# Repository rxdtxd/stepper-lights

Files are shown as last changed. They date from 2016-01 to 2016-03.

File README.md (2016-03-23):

# stepper-lights

## Table of Contents

* [Intro](#intro)
* [Using](#using)
  - [Warning](#warning)
  - [Overview](#overview)
  - [Schematics](#schematics)
  - [BOM](#bom)
  - [Fabrication files](#fabrication-files)
* [Modifying](#modifying)
  - [Toolchain](#toolchain)
  - [Custom symbols/footprints](#custom-symbolsfootprints)
* [Notes](#notes)
* [License](#license)

## Intro

Here's a project I did in early 2016 on controlling five stepper
motors with one AVR (Arduino Nano). Each channel has up/down
buttons and a potentiometer to control the speed.

## Using

### Warning

**I strongly suggest you do not try to recreate it verbatim, and use
as a guide at best.**

The schematics/layouts contained numerous glitches and therefore
impromptu fixes that were not propagated back to the design files.

Most notably, the used Arduino Nano symbol had its ADC pin order
reversed on the manufactured boards ([rev0.1](releases/tag/rev0.1)).
This required both hardware jumpering and software muckery, somewhat
reflected in [rev0.2](releases/tag/rev0.2).

Furthermore, the overall design leaves much to be desired. With
the current prices for Arduino Nano clones, **this should have been
a one-AVR-one-driver schematic**.

However, in the spirit of megalomania, I hereby release the files
under free licenses (for which see the bottom).

### Overview

There are two parts to the system: `controller` and `driver`:

```
             +-> driver
             |
             +-> driver
             |
controller --+-> driver
             |
             +-> driver
             |
             +-> driver
```

Communication is essentially single-directional SPI over RS422,
with the driver transmitting back a dummy message (i.e. no
feedback).

### Schematics

See [controller.png](schem/controller.png) and
[driver.png](schem/driver.png).

### BOM

See [controller.bom](schem/controller.bom) and
[driver.bom](schem/driver.bom).

Some mechanical components are not listed:

* push-buttons (OFF-(ON))
* power supply (24 V, 2+ A)
* power switch (OFF-ON)
* cooling fans (24 V)
* CAT6 cables and RJ45 connectors

### Fabrication files

See [fab](schem/fab) for gerbers and drill maps.

## Modifying

### Toolchain

The design files were produced on a [Arch](https://www.archlinux.org/)
GNU/Linux machine using [geda/gaf](http://www.geda-project.org/),
[pcb](http://pcb.geda-project.org/) and
[Emacs](https://www.gnu.org/software/emacs/).

AVR sources are built with [avr-gcc](https://gcc.gnu.org/). Arduino
is flashed with [avrdude](http://www.nongnu.org/avrdude/).

There are Makefiles for both schematics and code. Happy hacking!

### Custom symbols/footprints

...used in this project are available in my
[symbols](https://github.com/rxdtxd/geda-gschem-symbols-rxdtxd) and
[footprints](https://github.com/rxdtxd/geda-pcb-footprints-rxdtxd)
repos.

Note that these may have changed from the time they were used in the
project. I hope I was decent enough to change `symver`s and whatnot if
so.

## Notes

Some more unordered documentation is available in the [NOTES](NOTES)
file.

## License

Software in [src](src/) is licensed under [GPLv3](src/LICENSE). Hardware
designs in [schem](schem/) are licensed under [CERN OHL
v1.2](schem/LICENSE).

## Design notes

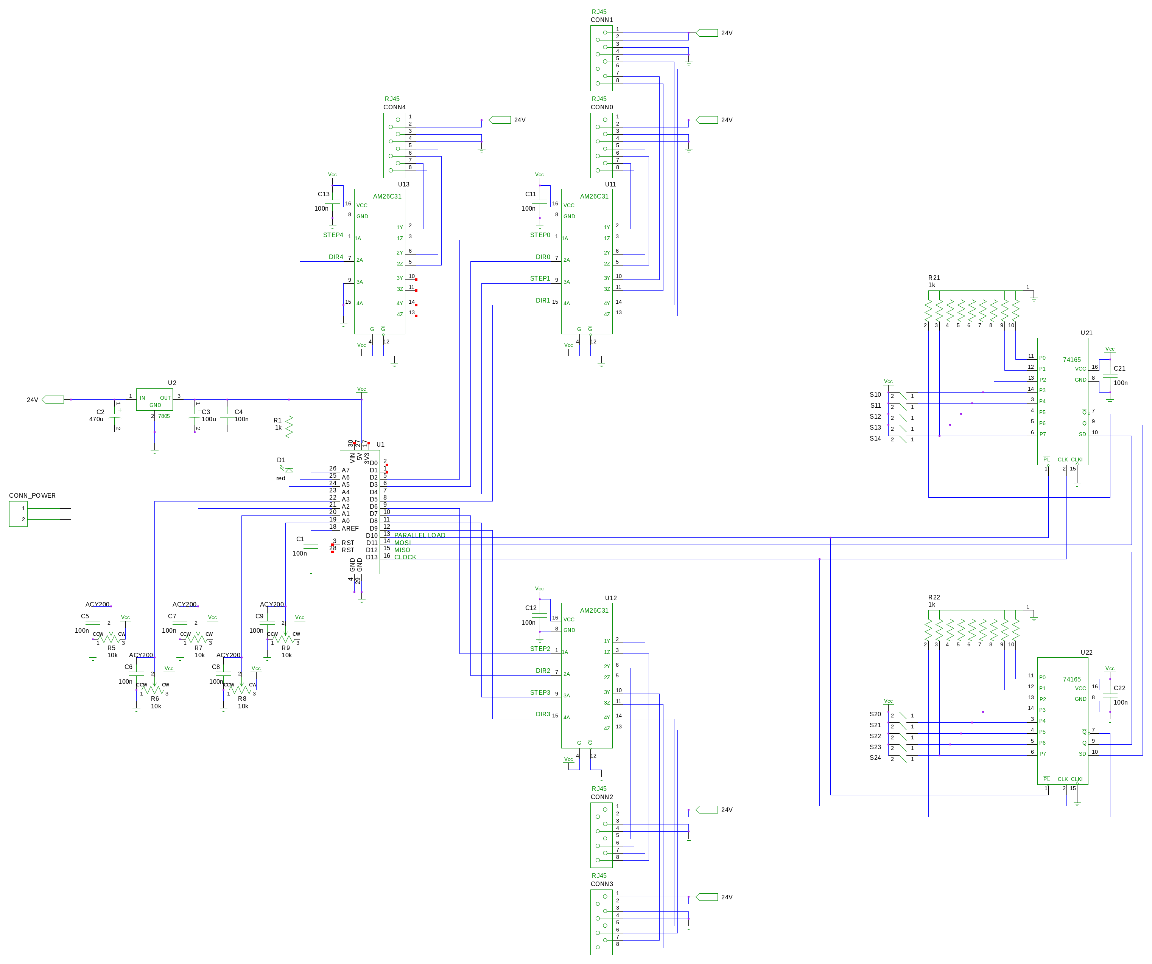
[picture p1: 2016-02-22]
schem/controller.png

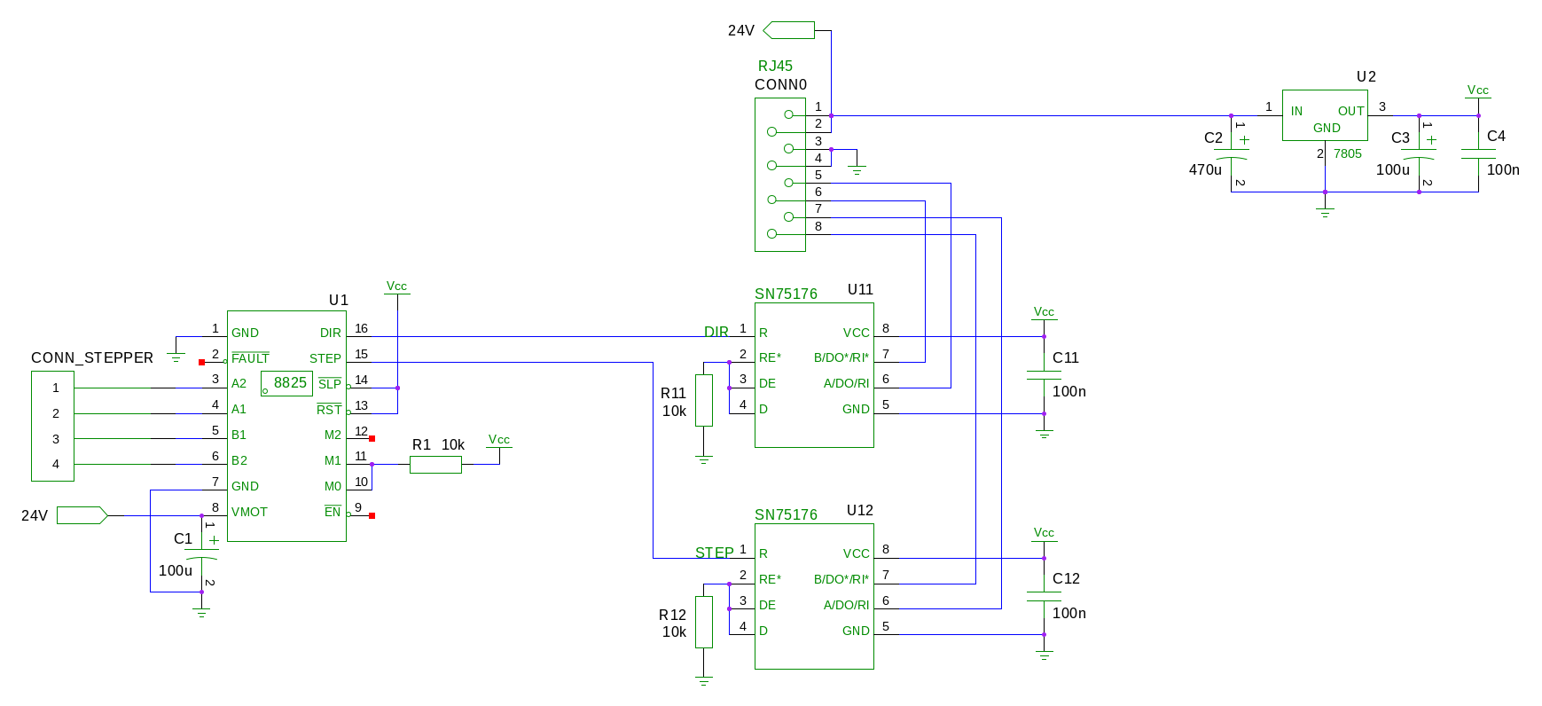
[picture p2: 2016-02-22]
schem/driver.png

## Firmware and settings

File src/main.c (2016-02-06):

// main.c
// stepper-lights

#include "pinout.h"

#include <stdbool.h>
#include <util/delay.h>

#include "adc.h"
#include "iocontrol.h"
#include "spi.h"
/* #include "uart.h" // debug terminal */

#define NMOTORS 5

#define RAMPCYCLES 8
#define RUNCYCLES 1024

// SPEED is a misnomer - it's actually the "period" between STEPs
// SPEEDMAX and SPEEDMIN have been switched places to reduce confusion
// in-code
#define SPEEDMAX 10
#define SPEEDMIN 100
#define SPEEDRANGE (SPEEDMIN-SPEEDMAX)

// maximum ADC-read value (depends on bit-resolution in adc_init())
#define POTMAX 1023

inline uint16_t motor_scale_speed (uint16_t potval) {
    uint32_t tmp;

    // HACK: pots soldered backwads on board
    potval = POTMAX - potval;
    
    // avoid stepper resonance regions (determined experimentally)
    tmp = (uint32_t)potval * SPEEDRANGE;
    potval = SPEEDMAX + (uint16_t)(tmp / POTMAX);

    return potval;
}

#define DIR_DOWN 0
#define DIR_UP 1

typedef struct {
    bool         isrunning; // whether currently running or not
    uint16_t     position;  // STEPs taken from top (0)
    bool         bu;        // button up pressed
    bool         bd;        // button down pressed
    uint16_t     pot;       // speed pot raw reading
    uint16_t     trgspeed;  // target speed
    uint16_t     curspeed;  // current speed
    uint16_t     counter;   // countdown timer for STEP phase toggling
} motor_t;


inline void motors_init (void) {
    set_output(MOTOR0_DDR, MOTOR0_STEP_DD);
    set_output(MOTOR0_DDR, MOTOR0_DIR_DD);
    output_low(MOTOR0_PORT, MOTOR0_STEP);
    output_low(MOTOR0_PORT, MOTOR0_DIR);

    set_output(MOTOR1_DDR, MOTOR1_STEP_DD);
    set_output(MOTOR1_DDR, MOTOR1_DIR_DD);
    output_low(MOTOR1_PORT, MOTOR1_STEP);
    output_low(MOTOR1_PORT, MOTOR1_DIR);

    set_output(MOTOR2_DDR, MOTOR2_STEP_DD);
    set_output(MOTOR2_DDR, MOTOR2_DIR_DD);
    output_low(MOTOR2_PORT, MOTOR2_STEP);
    output_low(MOTOR2_PORT, MOTOR2_DIR);

    set_output(MOTOR3_DDR, MOTOR3_STEP_DD);
    set_output(MOTOR3_DDR, MOTOR3_DIR_DD);
    output_low(MOTOR3_PORT, MOTOR3_STEP);
    output_low(MOTOR3_PORT, MOTOR3_DIR);

    set_output(MOTOR4_DDR, MOTOR4_STEP_DD);
    set_output(MOTOR4_DDR, MOTOR4_DIR_DD);
    output_low(MOTOR4_PORT, MOTOR4_STEP);
    output_low(MOTOR4_PORT, MOTOR4_DIR);

    return;
}

inline void motor_set_dir (uint8_t motor, uint8_t dir) {
    if (dir == DIR_DOWN) {
	if (motor == 0) { output_low(MOTOR0_PORT, MOTOR0_DIR); }
	else if (motor == 1) { output_low(MOTOR1_PORT, MOTOR1_DIR); }
	else if (motor == 2) { output_low(MOTOR2_PORT, MOTOR2_DIR); }
	else if (motor == 3) { output_low(MOTOR3_PORT, MOTOR3_DIR); }
	else if (motor == 4) { output_low(MOTOR4_PORT, MOTOR4_DIR); }
    } else {
	if (motor == 0) { output_high(MOTOR0_PORT, MOTOR0_DIR); }
	else if (motor == 1) { output_high(MOTOR1_PORT, MOTOR1_DIR); }
	else if (motor == 2) { output_high(MOTOR2_PORT, MOTOR2_DIR); }
	else if (motor == 3) { output_high(MOTOR3_PORT, MOTOR3_DIR); }
	else if (motor == 4) { output_high(MOTOR4_PORT, MOTOR4_DIR); }
    }
    
    return;
}

inline void motor_step (uint8_t motor) {
    if (motor == 0) { output_toggle(MOTOR0_PORT, MOTOR0_STEP); }
    else if (motor == 1) { output_toggle(MOTOR1_PORT, MOTOR1_STEP); }
    else if (motor == 2) { output_toggle(MOTOR2_PORT, MOTOR2_STEP); }
    else if (motor == 3) { output_toggle(MOTOR3_PORT, MOTOR3_STEP); }
    else if (motor == 4) { output_toggle(MOTOR4_PORT, MOTOR4_STEP); }

    return;
}

inline void shiftreg_load (void) {
    output_low(SPI_PORT, SPI_SS);
    _delay_us(0.02); // 74165's datasheet says 15 ns minimum
    output_high(SPI_PORT, SPI_SS);
    _delay_us(0.02);
    
    return;
}


int main (void) {
    uint8_t bu, bd;      // buttons up, buttons down (read-in buffers)
    uint8_t i;           // iterator
    uint8_t adcchan = 0;

    uint8_t ramp;
    uint16_t cycle;
    
    motor_t motor[NMOTORS];

    for (i = 0; i < NMOTORS; i++) {
	motor[i].isrunning = false;
	motor[i].position = 0;
	motor[i].bu = false;
	motor[i].bd = false;
	motor[i].pot = 0;
	motor[i].trgspeed = SPEEDMIN;
	motor[i].curspeed = SPEEDMIN;
	motor[i].counter = 0;
    }
    
    led_init();
    spi_init();
    adc_init();
    motors_init();

    /* // debug */
    /* uart_init(); */
    /* stdout = &uart_output; */

    adc_set_chan(adcchan);
    adc_start();

    while (1) {
	led_off();
	
	// keep the ADC running "in background"
	if ( !( adc_is_running() )) {
	    motor[adcchan].pot = adc_get();

	    if (motor[adcchan].bu != motor[adcchan].bd) {
		motor[adcchan].trgspeed =
		    motor_scale_speed(motor[adcchan].pot);
	    } else {
		motor[adcchan].trgspeed = SPEEDMIN;
	    }

	    adcchan++;
	    if (adcchan >= 5) adcchan = 0;

	    // HACK: lame jumpers
	    if (adcchan == 0) adc_set_chan(6);
	    if (adcchan == 1) adc_set_chan(1);
	    if (adcchan == 2) adc_set_chan(2);
	    if (adcchan == 3) adc_set_chan(3);
	    if (adcchan == 4) adc_set_chan(7);

	    adc_start();
	}

	// read in buttons
	shiftreg_load();
	bu = spi_transmit(SPI_TRANSMIT_DUMMY);
	bd = spi_transmit(SPI_TRANSMIT_DUMMY);
	for (i = 0; i < NMOTORS; i++) {
	    motor[i].bu = bit_is_set(bu, i) ? true : false;
	    motor[i].bd = bit_is_set(bd, i) ? true : false;

	    // both buttons pressed
	    if (motor[i].bu && motor[i].bd) {
		led_on();
		motor[i].trgspeed = SPEEDMIN;
	    }
	    
	    if (motor[i].bu != motor[i].bd) {
		motor[i].isrunning = true;
		
		// set dir
		if (motor[i].bu) {
		    motor_set_dir(i, DIR_UP);
		} else if (motor[i].bd) {
		    motor_set_dir(i, DIR_DOWN);
		}
	    }
	    // allow ramp-down
	    else if (motor[i].curspeed != motor[i].trgspeed) {
		motor[i].isrunning = true;
	    }
	    // mark as ok-to-stop
	    else if (motor[i].curspeed == SPEEDMIN) {
		motor[i].isrunning = false;
	    }
	}
       

	for (ramp = 0; ramp < RAMPCYCLES; ramp++) {
	    // push current speed towards target
	    for (i = 0; i < NMOTORS; i++) {
		if (motor[i].curspeed < motor[i].trgspeed) {
		    motor[i].curspeed += 1;
		}
		if (motor[i].curspeed > motor[i].trgspeed) {
		    motor[i].curspeed -= 1;
		}
	    }

	    // run at current speed
	    for (cycle = 0; cycle < RUNCYCLES; cycle++) {
		for (i = 0; i < NMOTORS; i++) {		
		    // either button pressed or ramp-down
		    if (motor[i].isrunning) {
			if (motor[i].counter > 0) {
			    motor[i].counter -= 1;
			} else {
			    // reset counter
			    motor[i].counter = motor[i].curspeed;
			    motor_step(i);
			}
		    }
		}
	    }
	}
    }
    return 0;
}

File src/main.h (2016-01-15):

// main.h
// pin definitions

#ifndef _MAIN_H_
#define _MAIN_H_

#include <avr/io.h>

#define F_CPU 16000000

// motor control - data direction
#define MOTORS_DDR DDRD
#define MOTOR0_STEP_DD DDD3
#define MOTOR0_DIR_DD DDD4
//#define MOTOR1_STEP_DD DDD?
//#define MOTOR1_DIR_DD DDD?
//#define MOTOR2_STEP_DD DDD?
//#define MOTOR2_DIR_DD DDD?
//#define MOTOR3_STEP_DD DDD?
//#define MOTOR3_DIR_DD DDD?
//#define MOTOR4_STEP_DD DDD?
//#define MOTOR4_DIR_DD DDD?

// motor control - output ports
#define MOTORS_PORT PORTD
#define MOTOR0_STEP PD3 // D3 on arduino
#define MOTOR0_DIR  PD4 // D4 on arduino
//#define MOTOR1_STEP PD?
//#define MOTOR1_DIR PD?
//#define MOTOR2_STEP PD?
//#define MOTOR2_DIR PD?
//#define MOTOR3_STEP PD?
//#define MOTOR3_DIR PD?
//#define MOTOR4_STEP PD?
//#define MOTOR4_DIR PD?


// leds
// TODO: remove
#define LED_0 0
#define LED_1 1
#define LEDS_DDR DDRD
#define LED0_DDR DDD5
#define LED1_DDR DDD6

#define LEDS_PORT PORTD
#define LEDBASE   PD5

#define leds_init() LEDS_DDR |= _BV(LED0_DDR)|_BV(LED1_DDR)
#define led_on(led)     LEDS_PORT &= ~(_BV( LEDBASE+led ))
#define led_off(led)    LEDS_PORT |=   _BV( LEDBASE+led )
#define led_toggle(led) LEDS_PORT ^=   _BV( LEDBASE+led )


// shift register to read in buttons - uses SPI
/* #define SHIFTREG_DDR     DDRB */
/* #define SHIFTREG_LOAD_DD DDB2 */

/* #define SHIFTREG_PORT PORTB */
/* #define SHIFTREG_LOAD PB2 // D10 on arduino (aka SPI_SS) */

#define SPI_DDR      DDRB
#define SPI_SS_DD    DDB2  // ~ slave select
#define SPI_MOSI_DD  DDB3  // 
#define SPI_MISO_DD  DDB4  // 
#define SPI_SCK_DD   DDB5  // clock

#define SPI_PORT     PORTB
#define SPI_SS       PORTB2   // D10
#define SPI_MOSI     PORTB3   // D11
#define SPI_SCK      PORTB5   // D13

#define SPI_PIN      PINB
#define SPI_MISO     PINB4   // D12


#endif /* _MAIN_H_ */

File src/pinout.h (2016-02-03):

// pin definitions

#ifndef _PINOUT_H_
#define _PINOUT_H_

#include <avr/io.h>

#define F_CPU 16000000UL

// motor control - data direction
#define MOTOR0_DDR     DDRD
#define MOTOR1_DDR     DDRD
#define MOTOR2_DDR     DDRD
#define MOTOR3_DDR     DDRB
#define MOTOR4_DDR     DDRC

#define MOTOR0_STEP_DD DDD2
#define MOTOR0_DIR_DD  DDD3
#define MOTOR1_STEP_DD DDD4
#define MOTOR1_DIR_DD  DDD5
#define MOTOR2_STEP_DD DDD6
#define MOTOR2_DIR_DD  DDD7
#define MOTOR3_STEP_DD DDB0
#define MOTOR3_DIR_DD  DDB1
#define MOTOR4_STEP_DD DDC0
#define MOTOR4_DIR_DD  DDC4

// motor control - output ports
#define MOTOR0_PORT    PORTD
#define MOTOR1_PORT    PORTD
#define MOTOR2_PORT    PORTD
#define MOTOR3_PORT    PORTB
#define MOTOR4_PORT    PORTC

#define MOTOR0_STEP    PORTD2  // D2
#define MOTOR0_DIR     PORTD3  // D3
#define MOTOR1_STEP    PORTD4  // D4
#define MOTOR1_DIR     PORTD5  // D5
#define MOTOR2_STEP    PORTD6  // D6
#define MOTOR2_DIR     PORTD7  // D7
#define MOTOR3_STEP    PORTB0  // D8
#define MOTOR3_DIR     PORTB1  // D9
#define MOTOR4_STEP    PORTC0  // A0
#define MOTOR4_DIR     PORTC4  // A4

// leds
#define LED_DDR DDRC
#define LED_DD DDC5

#define LED_PORT PORTC
#define LEDBASE  PORTC5  // A5

// TODO: move to iocontrol.h?
#define led_init()   LED_DDR |= _BV(LED_DD)
#define led_on()     LED_PORT &= ~(_BV( LEDBASE ))
#define led_off()    LED_PORT |=   _BV( LEDBASE )
#define led_toggle() LED_PORT ^=   _BV( LEDBASE )

// using SPI to read in shift registers (165s)
#define SPI_DDR      DDRB
#define SPI_SS_DD    DDB2    // ~ slave select
#define SPI_MOSI_DD  DDB3    // 
#define SPI_MISO_DD  DDB4    // 
#define SPI_SCK_DD   DDB5    // clock

#define SPI_PORT     PORTB
#define SPI_SS       PORTB2  // D10
#define SPI_MOSI     PORTB3  // D11
#define SPI_SCK      PORTB5  // D13

#define SPI_PIN      PINB
#define SPI_MISO     PINB4   // D12


#endif /* _PINOUT_H_ */

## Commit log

2016-01-11 First commit. Spin a stepper continuously.
    Arduino nano clone -> EasyDriver v4.4 -> stepper.
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2016-01-14 Track Arduino Nano symbol.
    [controller.sch]
2016-01-14 WIP: noise reading 165s
    [main.c, main.h]
2016-01-15 schem: some changes from y-day, dunno.
    [controller.sch]
2016-01-15 src: working SPI read from 165s.
    Use proper AVR-GCC delay instead of NIH fakedelay.
    Cleanup pinout defines.
    Figured out SPI polarity/phase.
    SPI data order: LSB first.
2016-01-18 schem: arduino nano & 165s.
    [controller.sch]
2016-01-18 src: half-working buttoned motor driving (ADC doesn't work).
    [main.c, pinout.h]
2016-01-18 ADC works - prescaler was missing.
    [main.c]
2016-01-19 src: `motorspeed` is uint16_t, make fakedelay() use that, too.
2016-01-19 schem: 7805 for power, pots connected to PINA{3-7}.
    [controller.sch]
2016-01-19 schem: stop tracking arduino-nano symbol (to kill gschem warning).
2016-01-19 schem: some controller changes (don't remember).
    [controller.sch]
2016-01-19 schem/driver: start tracking driver.sch
    [driver.sch]
2016-01-19 Move project NOTES.
    [controller.sch, driver.sch]
2016-01-19 schem/controller: good-night commit.
    [controller.sch]
2016-01-20 schem/controller: AM26C31 RS422 transmitters; RJ45 connectors; refdes'es for all symbols.
    [controller.sch]
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2016-01-21 src: fixups in pinout for using DRV8825 and 1 led.
    [main.c, pinout.h]
2016-01-21 src: motor_step() inline function, some code rearrangements, iterator var in fakedelay() is now volatile.
2016-01-21 src: Switch make optimisation from `s` to `2`.
2016-01-21 src: add uart.{c,h} for serial console, other minor edits.
2016-01-21 src: hard-limit unacceptable STEP pulse-width ranges (where stepper oscillates).
    [main.c]
2016-01-22 src: avoid stepper resonance regions by "scaling" read `speed` value.
    Formula is:
    scaled_speed = minval + (adc_speed/1023) * (maxval-minval)
    [main.c]
2016-01-22 schem/controller: add caps between pot wipers and ground.
    [controller.sch]
2016-01-22 schem/controller: connected 24V, 5V and 2 ground wires to RJ45 connectors.
    [controller.sch]
2016-01-22 schem/controller: actually, only send 24V. Will do 5V on driver-side.
    [controller.sch]
2016-01-22 NOTES: update RJ45 connector pinout to same as in previous 2 commits.
2016-01-22 schem/driver: full driver schematic.
    [driver.sch]
2016-01-25 schem/controller: add footprints to all symbols.
    [controller.sch]
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2016-01-25 schem/controller: proper POWER24V:1 net.
    [controller.sch]
2016-01-25 schem/controller: PCB with placed components (no routes yet).
2016-01-26 schem/controller: fully layed out board, 2 "wire jumpers".
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2016-01-27 schem/driver: POWER24V:1 net fix.
    [driver.sch]
2016-01-27 schem/driver: footprints for all elements.
    [driver.sch]
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2016-01-27 schem/controller: reworked mechanical design - wider, narrower board.
    Spacing between RJ45s increased, pots no longer "sit" on the board.
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2016-01-27 schem: gerbers for all layers of both boards.
    [controller.bottom.gbr, controller.bottommask.gbr, controller.bottompaste.gbr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]
2016-01-27 schem: renamed `gerber` dir to `fab`, added *.cnc files.
    [controller.bottom.gbr, controller.bottommask.gbr, controller.bottompaste.gbr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]
2016-01-27 schem/driver: modified pin/hole sizes, stopped tracking unneeded layers.
    [driver.bottom.gbr, driver.bottommask.gbr, driver.bottompaste.gbr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]
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2016-01-27 schem/controller: updated gerbers, stopped tracking unused layers.
    [controller.bottom.gbr, controller.bottommask.gbr, controller.bottompaste.gbr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]
2016-01-27 schem/controller: fixed layout name.
    [controller.bottom.gbr, controller.bottommask.gbr, controller.fab.gbr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]
2016-01-27 schem/controller: ground fill and a couple ground connections + gerber export.
    [controller.bottom.gbr, controller.bottommask.gbr, controller.fab.gbr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]
2016-01-29 schem/controller: change drill sizes where proper (from 0.8 mm to 1 mm).
2016-01-29 schem/driver: post-manuf fix-ups (short between power and ground, drill sizes).
2016-01-31 schem: give tab as separator to `column`.
    Otherwise footprints with spaces in them mangle up the table.
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2016-01-31 README: note about parts missing in BOM.
2016-02-01 schem/controller: change a few footprints and re-annotate.
    [controller.sch]
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2016-02-01 schem: updated gerbers using new Makefile.
    [controller.bottom.gbr, controller.bottommask.gbr, controller.fab.gbr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]
2016-02-01 schem/controller: bottom connects on 24V and GND pins for RJ45s.
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2016-02-01 schem: gerbers from y-day's changes.
    [controller.bottom.gbr, controller.bottommask.gbr, controller.fab.gbr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]
2016-02-02 schem/driver: updated footprints.
    [driver.sch]
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2016-02-02 schem: updated gerbers.
    [controller.bottom.gbr, controller.bottommask.gbr, controller.fab.gbr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]
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2016-02-03 schem/controller: proper arduino symbol.
    [controller.sch]
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2016-02-03 schem/controller: _really_ proper arduino symbol.
    [controller.sch]
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2016-02-03 src: cleanup, read in all 5 ADC channels.
2016-02-03 src: working button reading for all 5 motors + both-buttons-pressed detection.
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2016-02-03 src: move led_off() so it's more visible when on.
2016-02-03 src: using ADC{6,7} (PORTC{6,7}) for IO is impossible, so hack to use 0 and 4.
    Goddamn symbol downloaded from internets had reversed
    "analog input port (of arduinoland)".
    In addition: looks like assigning stuff like
    port = MOTOR0_PORT
    pin = MOTOR0_DIR
    doesn't work. :/
    [main.c, pinout.h]
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2016-02-03 src: working motor_step() with same hardcoded motor selection.
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2016-02-05 src: increase counter 64 times (1023 * 64 < max(uint16_t)).
    Not sure how big this magicnum should be, can't test since board is away on preview. :/
2016-02-05 src: minor optimisations, ADC within stepping loop makes system too slow.
    Running ADC within stepping cycle is counter-productive, since
    it takes too long and slows down the entire system too
    much.
    [main.c]
2016-02-05 src: adc.{c,h} were not tracked for some reason.
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2016-02-05 src: slight optimisation - do "speed adjustment" out of motor-counter loop.
2016-02-05 src: replace NIH pressed() with bit_is_set().
    [main.c]
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2016-02-05 src: rename SPEEDMAX to SPEEDMIN to avoid confusion (yeah, right).
    [main.c]
2016-02-05 src: move motor_scale_speed() so it's near the #defines.
2016-02-05 src: some refactoring (moved led_off() and both-buttons-pressed check).
2016-02-06 src: reverse pot direction (soldered backwards + some comments.
    [main.c]
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2016-02-06 schem: Makefile with `all` rule.
    [controller.bottom.gbr, controller.bottommask.gbr, controller.fab.gbr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]
2016-02-22 schem/controller: make footprint/package fields invisible + arduino's refdes is U1 again (was U?).
    [controller.sch]
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2016-02-22 schem: fix schematics for PNG export.
    [controller.sch, driver.sch]
2016-02-22 schem: PNG schematics (exported with `make png` ^_^).
    I lub gEDA.
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
